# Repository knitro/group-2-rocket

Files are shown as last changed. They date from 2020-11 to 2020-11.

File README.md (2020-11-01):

# Model Rocket System
This repository contains all the files associated with the planning, design and implementation of a model rocket avionics system. 

## Hardware

### 3D Models
The folder contains the STL files for the various components that were modelled and printed for the rocket.
The parts included are:
- Gimbal
- Gimbal adaptor
- Nose cone
- Rocket body
- Rocket stand

### Avionics System
This contains the files and designs for the avionics system that will be onboard. This includes things such as the bill of materials, PCB schematics and the libraries used for the different boards.

### Base Station System
Contains the schematic and PCB layout used for the base station system. 

### Open Rocket Simulation
Contains the Open Rocket simulation for the designed rocket. In the files it contains the dimensions for the different components and weights. 

## Firmware

## Avionics System Firmware
This contains the code used for the avionics system. This includes things such as the libraries used for the different components,the test code for the different sensors and the source files for them.

### Base Station Firmware
This contains the code that will be used by the base station.

## Documentation

### Project Requirements
This contains documents which specify the requirements for the project as outlined by the stakeholder. This includes things such as the health and safety plan, lab safety plan and thorough definition of the project requirements. In the project requirement document it discusses the purpose and scope of the project, and what we planned to achieve before the end of the project.

### Architecture Design
This section contains a document which describes the architectural design of the rocket and the various systems. A proof of concept is developed using the considerations outlined in the project requirements.

### Retrospective Images
This contains the images from the retrospectives taken at the end of every sprint. In them they show what has been going well, what could be improved and other opinions of the team on this project.

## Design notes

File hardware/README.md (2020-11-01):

The software for the avionics system and base station is developed using the PlatformIO ecosystem which is built on top of the Visual Studio Code IDE. The board used by the avionics system is the Adafuit Feather STM32F405, and the board used by the base station is the Arduino Nano ATmega328.

The hardware for the avionics system is composed from several different components which have different functions. To allow for easier interfacing with the the hardware several software libraries are used. 

The different components used in the avionics system, as the libraries required are listed below:

- BMP280 (Barometer): Adafruit BMP280 Library https://github.com/adafruit/Adafruit_BMP280_Library
- BNO055 (9 Axis IMU): Adafruit BNO055 Library https://github.com/adafruit/Adafruit_BNO055
- NEO-M8N: NeoGPS https://github.com/SlashDevin/NeoGPS
- RFM95W: RadioHead Library http://www.airspayce.com/mikem/arduino/RadioHead/index.html

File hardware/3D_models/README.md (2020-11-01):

This folder contains the 3D model used to create the rocket gimbal, rocket body, nose cone and the rocket stand.

The 3D models were developed using a mixture of Solid Edge and Blender, with the files being exported as .stl for 3D printing.

All parts were printed using PLA filament, although other filaments may be preferable for increased strength. 

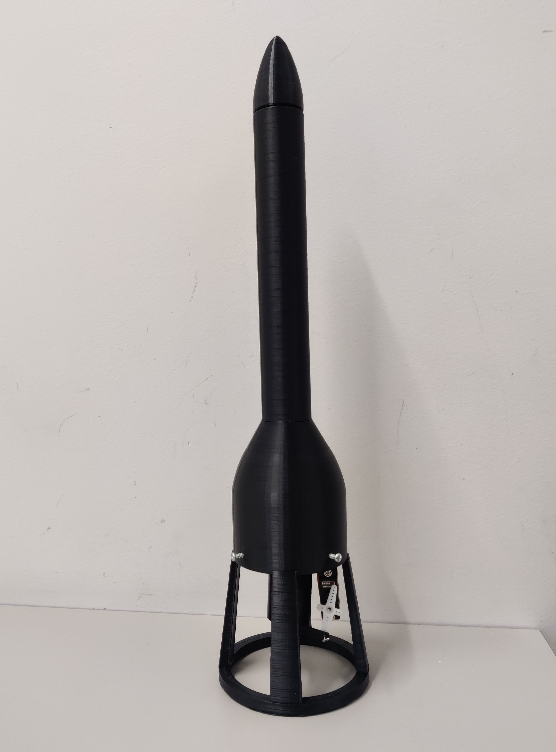
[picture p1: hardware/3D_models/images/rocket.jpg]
Assembled Rocket


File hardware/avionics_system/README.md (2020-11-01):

Throughout the project two hardware systems were developed- a prototype system and a version intended for use in the actual rocket. The prototype system was developed using a breadboard and breakout boards for initial developement and testing of code. For the second system, a schematic and corresponding PCB layout was developed, with the intention of using this design inside the model rocket. Due to time constraints, the PCB was not able to be printed and populated. Although the electronics were not assembled, all of the information required for assembly including BOM and PCB designs have been included in the hardware section of the repository.

### Pinout for prototype avionics system design:
The prototype system used an Adafruit Feather F4 in conjunction with breakout boards for the different sensors required in the avionics system. Below are the pin connections for the prototype avionics system. Note that:
- BMP280 is barometer module using SPI interface
- RFM95 is LoRa transceiver using SPI interface
- BNO055 is IMU using I2C interface
- BMP280 and RFM95 are connnected to the same SPI bus (SPI2)

| Feather Pin |  MCU Reference | Pin Function | Device Connection |
| --- | --- | --- | --- |
| A0 | PA4 | Analog in | LED |
| A1 | PA5 | Analog in | LED |
| A2 | PA6 | Analog in | LED |
| A3 | PA7 | Analog in | LED |
| A4 | PC4 | Analog in | LED |
| A5 | PC5 | Analog in | LED |
| SCK | PB13 | SPI2_SCK | SCK of BMP208 & RFM95 |
| MOSI | PB14 | SPI2_MOSI | MOSI of BMP208 & RFM95 | 
| MISO | PB15 | SPI2_MISO | MISO of BMP208 & RFM95 |
| RX | PB11 | UART3_RX | TX of NEO-M8N |
| TX | PB10 | UART3_TX | RX of NEO-M8N |
| B0 | BOOT0 | Boot0 Pin | Unused |
| SDA | PB7 | I2C1_SDA | SDA of BNO055 |
| SCL | PB6 | I2C1_SCL | SCL of BNO055 |  
| 5 | PC7 | Digital GPIO | RST of RFM95 |
| 6 | PC6 | Digital GPIO | LED |
| 9 | PB8 | Digital GPIO | INT of BNO055 |
| 10 | PB9 | Digital GPIO | G1 of RFM95 |
| 11 | PC3 | Digital GPIO (SPI Slave Select) | SPI2_SS1 of BMP208 |
| 12 | PC2 | Digital GPIO | DIO0 of RFM95 |
| 13 | PC1 | Digital GPIO (SPI Slave Select) | SPI2_SS2 of RFM95 |
| SDIO_D0 | PC8 | SD Card | SD Card | 
| SDIO_D1 | PC9 | SD Card | SD Card |
| SDIO_D2 | PC10 | SD Card | SD Card |
| SDIO_D3 | PC11 | SD Card | SD Card |
| SDIO_CLK | PC12 | SD Card | SD Card |
| SDIO_CMD | PD2 | SD Card | SD Card |
| SD_DETECT | PB12 | SD Card | SD Card |

### Pinout description for avionics system PCB design:
The table below describes the pin connections of the microcontroller and the other sensors on the avionics board. For a full connection diagram, refer to the schematic of the main avionics board.

| MCU Pin |  MCU Reference | Pin Requirements | Pin Function |
|---|---|---|---|
| 1 | VBAT | Battery input voltage (RTC) | Power |
| 2 | PC13 | Unused | - |
| 3 | PC14 | Unused | - |
| 4 | PC15 | Heartbeat LED | GPIO Out |
| 5 | PHO | Crystal input | Crystal |
| 6 | PH1 | Crystal output | Crystal |
| 7 | NRST | RESET pin | Reset |
| 8 | PC0 | Unused | - |
| 9 | PC1 | Unused | - |
| 10 | PC2 | Unused | - |
| 11 | PC3 | Unused | - |
| 12 | VSSA | Analog ground | Power |
| 13 | VDDA | Analog voltage supply | Power |
| 14 | PA0 | Battery voltage sense | GPIO Analog |
| 15 | PA1 | Reset for RFM95 | GPIO Out |
| 16 | PA2 | UART2_TX for GPS | UART |
| 17 | PA3 | UART2_RX for GPS | UART |
| 18 | VSS | Ground | Power |
| 19 | VDD | 3.3V supply | Power |
| 20 | PA4 | SPI1_NSS for Barometer | SPI |
| 21 | PA5 | SPI1_SCK for Barometer | SPI |
| 22 | PA6 | SPI1_MISO for Barometer | SPI |
| 23 | PA7 | SPI1_MOSI for Barometer | SPI |
| 24 | PC4 | IMU Interrupt 1 | External Interrupt (GPIO Input) |
| 25 | PC5 | IMU Interrupt 2 | External Interrupt (GPIO Input) |
| 26 | PB0 | SERVO 1 PWM | PWM |
| 27 | PB1 | Servo 2 PWM | PWM |
| 28 | PB2 | BOOT1 | BOOT1 pin |
| 29 | PB10 | I2C2_SCL for IMU		| I2C |
| 30 | PB11 | I2C2_SDA for IMU		| I2C |
| 31 | VCAP | Internal regulator capacitor  | Power |
| 32 | VDD | 3.3V Supply | Power |
| 33 | PB12 | SPI2_NSS for RFM95 | SPI |
| 34 | PB13 | SPI2_SCK for RFM95 | SPI |
| 35 | PB14 | SPI2_MISO for RFM95 | SPI |
| 36 | PB15 | SPI2_MOSI for RFM95 | SPI |
| 37 | PC6 | UART6_TX (Breakout) | UART |
| 38 | PC7 | UART6_RX | UART (Breakout) |
| 39 | PC8 | SDIO_D0 for SD Card | SDIO |
| 40 | PC9 | SDIO_D1 for SD Card | SDIO |
| 41 | PA8 | RFM95 Interrupt | External Interrupt (GPIO Input) |
| 42 | PA9 | USB VBUS | USB OTG |
| 43 | PA10 | USB ID | USB OTG |
| 44 | PA11 | USB DM | USB OTG |
| 45 | PA12 | USB DP | USB OTG |
| 46 | PA13 | SWDIO for JTAG | ARM_JTAG |
| 47 | VCAP | Internal regulator capacitor  | Power |
| 48 | VDD | 3.3V Supply | Power |
| 49 | PA14 | SWCLK for JTAG | JTAG |
| 50 | PA15 | Unused | - |
| 51 | PC10 | SDIO_D2 for SD Card | SDIO |
| 52 | PC11 | SDIO_D3 for SD Card | SDIO |
| 53 | PC12 | SDIO_CK for SD Card | SDIO |
| 54 | PD2 | SDIO_CMD for SD Card | SDIO |
| 55 | PB3 | SWO for JTAG | JTAG |
| 56 | PB4 | Unused | - |
| 57 | PB5 | Eject 1 for Parachute | GPIO Output |
| 58 | PB6 | Eject 2 for Parachute | GPIO Output |
| 59 | PB7 | Eject 3 for Parachute | GPIO Output |
| 60 | BOOT0 | BOOT0 for programming | BOOT0 |
| 61 | PB8 | Unused | - |
| 62 | PB9 | SD_DETECT for SD card | GPIO Input |
| 63 | VSS | Ground | Power |
| 64 | VDD | 3.3V Supply | Power |

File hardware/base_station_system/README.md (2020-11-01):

A prototype base station system was developed in conjunction with the developement of the prototype avionics system. This system simply consists of an Arduino Uno board connected to a RFM95 LoRa module for communication with the avionics system.

### Pinout for base station prototype:

Below shows the pin connections of the base station. It simply consists of a RFM95 transceiver module connected to an Arduino Uno/Nano (or compatible) via an SPi interface.

| Arduino Pin | MCU Reference | Pin Function | Device Connection |
| --- | --- | --- | --- |
| 13 | PB5 | SCK | SCK of RFM95 |
| 12 | PB4 | MISO | MISO of RFM95 |
| 11 | PB3 | MOSI | MOSI of RFM95 |
| 10 | PB2 | SS | CS of RFM95 |
| 9 | PB1 | Digital GPIO | RESET of RFM95 |
| 3 | PD3 | Digital GPIO | DIO1 of RFM95 |
| 2 | PD2 | Digital GPIO | DIO0 of RFM95 |

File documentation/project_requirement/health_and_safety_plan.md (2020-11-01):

# ENGR 301: Safety Plan Living Document

## Introduction:

The aim of this document is to layout the safety plan draft for the avionics system Group 2 will build. This will include listing the project requirements that create risk of bodily harm, and the plan to mitigate those risks.

This is to be adjusted according to changes in the working environment, as well as the wider society. Due to unsettling times resulting from COVID-19, health and safety should be of most concern, even if the situations that we may be in are constantly changing within both the context of the project, and our own personal lives. *See section 2 for more details.*

## Contents:

1. **The Rocket**
2. **COVID-19**
    * 2.1 Alert Level 1
    * 2.2 Alert Level 2
    * 2.3 Alert Level 3
    * 2.4 Alert Level 4
3. **Launch Details**
    * 3.1 Travel Plan
    * 3.2 Environment
    * 3.3 Equipment
    * 3.4 Supervision
    * 3.5 Launch
    * 3.6 Unforeseen Events
        * 3.6.1 Members of the public
        * 3.6.2 Faulty Components and Equipment
4. **Appendices**
    * Appendix A: Risk and Mitigations
    * Appendix B: CAA of NZ Regulations Part 101.7
5. **Bibliography**

## 1. The Rocket:

As of this stage, the specific form of the rocket is undeterminable; however, general aspects that the rocket have been outlined, and safe procedures for those aspects determined.

The rocket will use either an electric or solid-fuel motor; in the case of the solid fuel motor, additional risks are presented. The solid fuel motor used, of which is limited to the C and D classifications, is obtained as a complete certified product by the given manufacturer. The motor will not be modified, or used, in any way other than that outlined by the manufacturer. The engine must never be exposed to any ignition source other than that of the launch platform, and for this case, only when carrying out the launch event. Only an electrical ignition system can be used for the ignition of the rocket, as per the NZ Rocketry Association's safety code for rockets utilizing class A-F motors.

The rocket's expected maximum altitude after launching has not yet been determined. The distance the rocket may drift after launch, due to wind, may resultantly not be determined. Regardless, an exclusion zone around the rocket launch site must be established before launching; only personnel directly tasked with the launch of the rocket may be permitted within this zone. Minimizing the risk to non-vital personnel is paramount.

The NZ Rocketry Association's safety code also states that materials used for exterior features of the rocket (nose, body, and fins) must be lightweight and non metal. This is to minimize potential injury in the event that the rocket falls, or otherwise collides, with a person.

## 2. COVID-19:

An issue that has arisen during the initialization of this project has been COVID-19. This situation is evolving as the newly introduced COVID-19 Alert System [1] forces changes upon the workflow on the project. To plan and comply with each alert system, the guidelines below must be followed by all team members on top of any requirements from the official alert system [1], and any other requirements listed in this document.

### 2.1. Alert Level 1:
*Prepare Stage: The disease is contained in New Zealand* 

* Any team member who feels unwell should stay home immediately, while contacting everyone else in the team to let them know. A time when they started to feel ill should be disclosed during this contact.
* When meeting in person, all team members must engage in physical distancing as per the recommended from the NZ Government.

### 2.2. Alert Level 2:
*Reduce Stage: The disease is contained, but the risk of community transmission remains*

* Everything from Alert Level 2 and..
* All launches must be performed where nobody else from the public is present.

### 2.3. Alert Level 3:
*Restrict Stage: High risk the disease is not contained*

* Everything from Alert Level 2 and below and ..
* All project work must be done online with no exceptions.
* All meetings must be performed online.
* Any launches are to be postponed until a lower alert level is reached. 

### 2.4. Alert Level 4:
*Lockdown Stage: Likely that disease is not contained*

* Everything from Alert Level 3 and below and ..
* Requirements and deadlines to be extended to assist in the mental health of all team members from the stress.

## 3. Launch Details:

An issue that has arisen during the initialization of this project has been COVID-19. This situation is evolving as the newly introduced COVID-19 Alert System [1] forces changes upon the workflow on the project. To plan and comply with each alert system, the guidelines below must be followed by all team members on top of any requirements from the official alert system [1], and any other requirements listed in this document.

### 3.1. Travel Plan:

To ensure the safe transportation of all team members and the rocket, the procedures listed must be followed:

**Team Members:** <br>
* A designated university staff member must be contacted prior to the travel, citing exact time, date and location of the launch, and the arrival time after the launch.
    * The contact details must be readily available for all team members.
* Time, date and the location of where we are going to launch must be written in the Mattermost for everyone to reference against.
* There must be an established meeting place for the situation where any member is lost. This location must be determined, and known to all members, prior to the rocket's launch.
    * This meeting place must have reception and/or internet connection that is accessible by all team members. This is to ensure everyone present is able to make contact with appropriate team members or university staff.
* Everyone must be able to contact each other through mobile means (such as text/messenger apps) in the case that a team member is missing.
    * If contact through these means is unavailable (such as lack of reception), then everyone must meet at the designated meeting place.
* In the event that it is unavailable to meet with or contact a team member, the designated university staff must be contacted to explain the situation.
* If the team members do not arrive at the specified time, the designated university staff must take emergency action.

**Rocket:** <br>
* The rocket must be transported, such that the engine is not ignited during transport.
    * [Engine specifications here with heat that the engine combusts, ways to mitigate this]
* The rocket must be transported, such that the rocket does not injure anyone through physical contact.
    * This is to be resolved through transporting the rocket such that the rocket should not be able to be moved while in transport.
    * [Add exact transportation implementation of the rocket here]

### 3.2. Environment:

All relevant regulations must be met to ensure that the rocket launch is as safe as possible for the team members, as well as the wider community and environment. These include the following:
* CAA 101.157 - The rocket shall not be launched given that there are clouds that cover more than half of the sky (See Appendix B)
* CAA 101.158 - The rocket should not be launched during the night (See Appendix C)

To ensure these regulations are met, the following assessment of the environment must be performed before launch:
* The rocket is to be only launched during the day, with more than half of the sky being visible, and not obstructed by clouds.
    * This is to ensure the rocket's location, regardless of GPS tracking, can be observed and followed during the entire rocket launching process.
* Check for any precipitation. The presence of any will lead to the cancellation of the launch. 
    * This is due to the possible case that the precipitation disallows the rocket to successfully launch, creating a situation where the rocket has not launched when expected.
* Wind speeds and gusts must be checked to not exceed ([some_value] km/h, [some_value] km/h). 
    * This is due to the possible case that the ignited rocket will spread the ignition flames to uncontrollable levels.
    * This is also to ensure that the rocket is still able to have a controlled ascent up, and descent down, without leaving the specified premises.

Wind Speeds, weather and precipitation chance data are all to be collected via the AccuWeather and MetService before launch day, and before launch. 
*  https://www.accuweather.com/
*  https://www.metservice.com/
If the weather does not permit and/or appear to not be permittable (such as high chance of precipitation) during any of these stages, the launch should be cancelled or postponed immediately.

To avoid any damage in the environment where the launch is taking place, it must be ensured that:
* The area is clear of anyone else other than team members and/or other supporting staff.
* The area around the rocket launching position must be clear of debris.
* The area that the launch of the rocket is taking place must be clear from any obstructions that may cause disruptions if interacted with, such as powerlines.
* Potential landing areas downwind from the launch site must be free of obstructions that could be damaged and/or interact with the rocket. The potential landing area must be calculated before each launch, taking into account dynamic factors such as wind speed, rocket motor burn time, expected altitude and other factors. The landing area will be extremely large so that safety is not at risk and the ability to recover the rocket is almost ensured.

If any of these conditions cannot be fully met, the launch must be postponed or cancelled entirely.

To ensure no member of the public walks in during the launch sequence, or during flight, there shall be 3-4 team members covering all possible entrances at the maximum distances into the launch site, advising and ensuring nobody enters until the launch has finished.
If anybody disregards these orders for any reason, the launch must be cancelled or postponed if the launch has not been performed yet.

### 3.3. Equipment

The following equipment is to be taken to the launch. These must all be checked off prior to, during, and after being at the launch site. This is to ensure all items are accounted for, and that any dangerous or safety related equipment for other teams are still available for use, and aren't left as a risk to the general public.

| Equipment 	| Owner 	| Purpose |
|---	|---|--- |
| Rocket 	| ? 	| To ensure we have something to actually launch. |
| First Aid Kit 	| School of Engineering and Computer Science at Victoria University of Wellington 	| This is to assist in the case of an injury from a team member, or a member in the public. |
| Fire Extinguisher 	| School of Engineering and Computer Science at Victoria University of Wellington 	| This is to assist in the case of a fire. |
| Hi-Vis Vests 	| School of Engineering and Computer Science at Victoria University of Wellington 	| This is to assist in finding and distinguishing team members so that they are visible at all times. |
| Safety Goggles 	| School of Engineering and Computer Science at Victoria University of Wellington 	| This is to ensure the protection of all participants eyes from fires, explosions or transport of potentially dangerous materials 	|
| Personal Mobile Phones 	| Team Members 	| This is for communications and checking weather. |
| Rail Launch Pad 	| ? 	| This is to ensure the stability of the rocket prior to launch. |
| Laptop 	| Team Members 	| This is such that data is able to be intercepted, and recorded from the rocket's antenna. It is also used for checking weather data. |
| Ignition Switch 	| ? 	| This is so the rocket is able to be launched. 	 |
| Tool Kit | School of Engineering and Computer Science at Victoria University of Wellington | This is to ensure in the case the rocket is damaged, it can be repaired. |
| Spare Repair Gear for the Rocket | ? | This is to ensure in the case the rocket is damaged, it can be repaired using the spare repair gear. | 

### 3.4. Supervision

All launches will be supervised by the client. The client for this design and is a member of the NZ Model Rocketry Association.
The client will be responsible for approving the launch and launching the rocket, no one else may launch the rocket. All motors and propellant will be transported to and from the launch site by the client. The rocket will be launched from a launch pad and rail provided by the client.

### 3.5. Launch

The launch of the rocket poses multiple risks to team members, and members of the general public; minimizing these risks is paramount.

In accordance with the NZ Rocketry Association, individuals are free to launch rockets using class A to D motors, provided they have the permission of the owner of the launch site. No greater authority needs to be informed of the rocket's launch.

The immediate launch site must be safe from hazards before a launch may be prepared; this includes direct (e.g. sharp objects) and indirect (e.g. flammable materials) hazards that may harm team members. In these conditions, members of the general public should not be present; however, these hazards should be considered as potential risks for the general public as well.

Solid fuel motors pose the greatest risk at launch; flammable debris, such as dry grass, may ignite as a result of the motor's burn. The immediate area within 3m of the launch pad must be clear of any flammable materials. If this is not achievable, a fire resistant deflection material may be place immediately underneath the launch pad. All personnel must wear suitable PPE in preparation for the launch; namely safety glasses.

Personnel related to the rocket launch should be clear of the rocket at the time of launch. When the area is deemed clear of hazards, and all personnel safely distanced from rocket, a countdown will commence to make all personnel aware of the eminent launch. This countdown will provide a generous, and safe amount of time for all personnel; any member of the team may cancel the launch at any point during the countdown, at which point the safety interlocks will be re-enabled.

In the event of a misfire, launch pad safety interlocks must be enabled. The rocket is not to be approached for at least 60 seconds, at which point only the client may approach the launch pad for inspection.

### 3.6. Unforeseen Events

#### 3.6.1 Members of the Public

To ensure the safety of the members of the public, the following must be performed:
* Any member of the public entering the premises of the launch must be stopped by a team member to the best of their ability. If the closest team member is unable to communicate with that member of the public under any circumstance, another team member must approach the given member of the public to discuss about the rocket launch, and inform them of the associated risks.
* If a member of the public would enter the premise of the launch site, the launch must be postponed until the member of the public leaves the premises.
* If a member of the public is unwilling to listen to the team member, the client must be contacted ASAP to discuss the situation with the member of the public.
* If, for any reason, a member of the public decides to not listen to the warnings and communications of the team members, either actively or inactively, the launch of the rocket must be postponed if possible, until the issue is resolved with the client and the member of the public.

#### 3.6.2 Faulty Components and Equipment

To ensure the safe launch of the rocket, the following procedures must take place if there appears to be faulty equipment:
* If the rocket is physically damaged/suspected to have sustained damage during transportation, the motor must be removed before being inspected.
    * If the rocket has sustained physical damage, it must be determined if the rocket is still safe to launch or not. If the rocket can not be suitably repaired in-the-field, such that it could perform identically to how it would have prior to the damage, the launching of the rocket must be postponed until proper repairs have been completed.
    * If any electronics are broken alongside the physical body of the rocket, then the launch is to be postponed until the fix can be made.
    * If the fix cannot be made to either the physical rocket or the electronics, the launch is to be cancelled until further notice.
* If anything corresponding to the launch is faulty (such as failure of motor ignition or lack of combustion), all members near the launch must promptly relocate to a designated protected area, wait a minimum of 2 minutes, and then allow the client to approach and assess the situation.

## 3.7 Lab Risks:

When constructing the rocket in the lab, there are several important risks to account for.

* When working on computers for coding, regular breaks must be taken to reduce the chances of repetitive strain injury (RSI) and any strains to the eyes.
* When creating the rocket, the working area must be clean. This means that:
    * The floors must be clean such that cables and wires do not trip anyone up.
    * Furthermore, there should not be any sharp objects on the ground in case anyone does trip.
    * There must be sufficient air flow when soldering, such as a room air conditioning and a small fan at the soldering station.
    * Contact to wall outlets/230VAC supply should never be made under any circumstances; connections to these outlets should never be exposed.
    * The maximum voltage of any circuit, under prototyping conditions or other, should never exceed 60V.

# 4 Appendix:

## Appendix A:
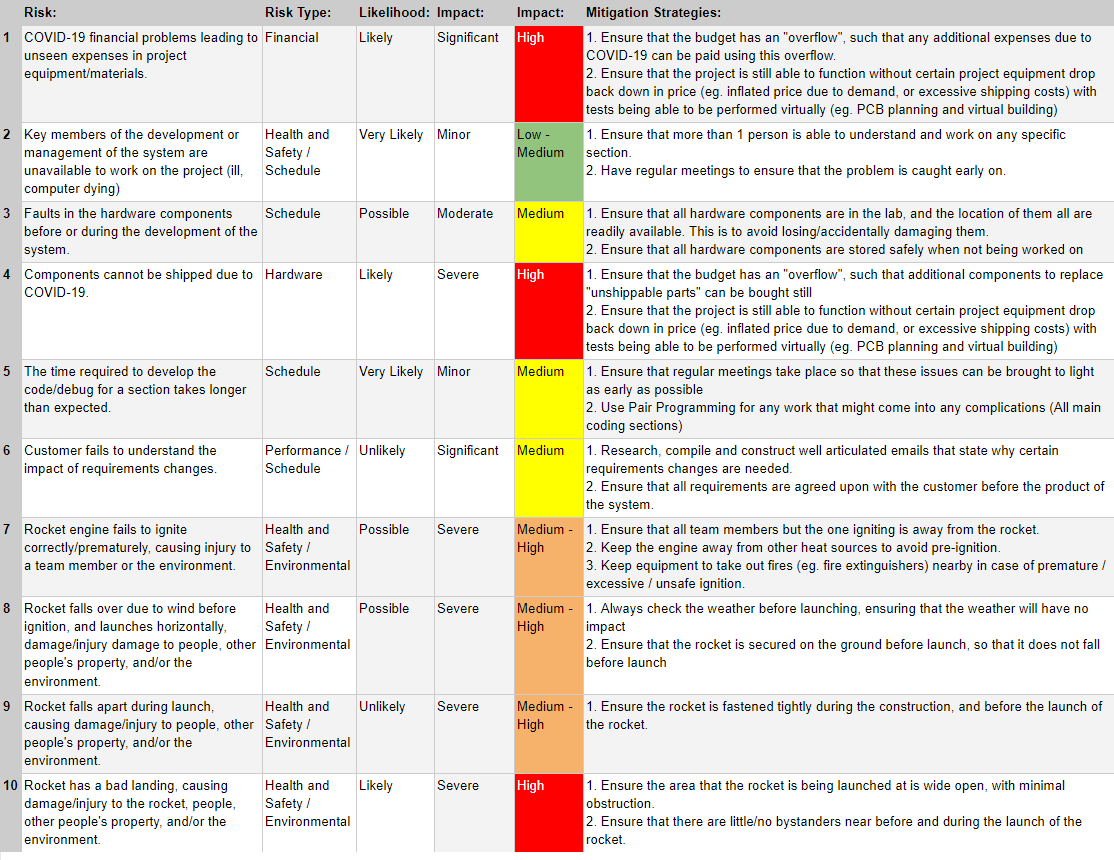
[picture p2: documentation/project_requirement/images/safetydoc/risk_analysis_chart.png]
Appendix Image


## Appendix B:
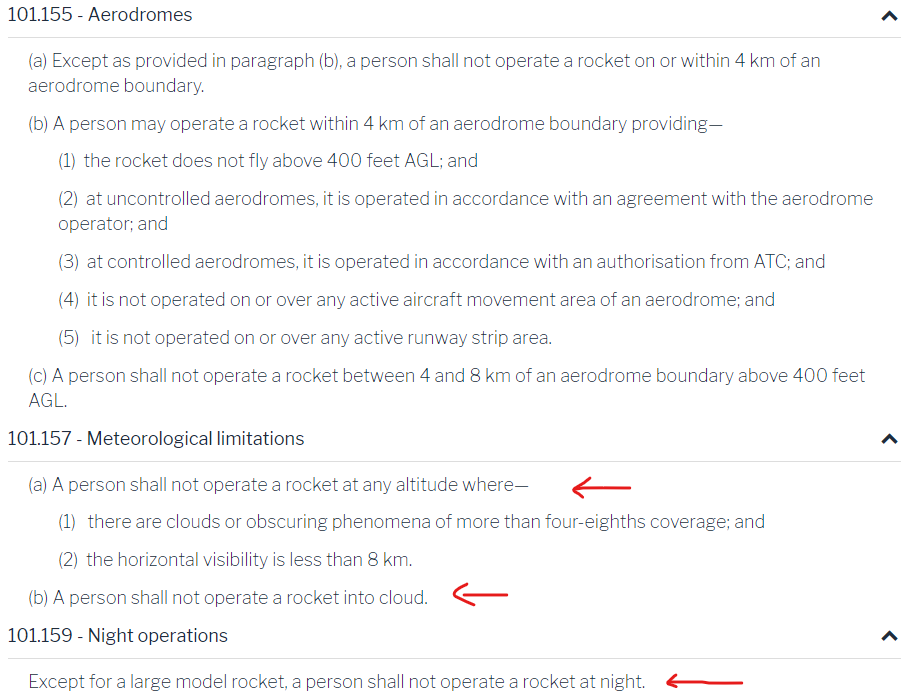
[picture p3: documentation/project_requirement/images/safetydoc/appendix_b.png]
Appendix Image


# 5. Bibliography: <br>
[1] https://covid19.govt.nz/alert-system/
[2] https://www.nzrocketry.org.nz/rocketry/rocket-safety

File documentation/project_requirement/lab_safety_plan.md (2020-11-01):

# Lab Safety Plan

*Last Update: 07/08/2020*

## Introduction

The aim of this document is to layout a Health and Safety Plan for the hardware development of the rocket.
The development of the rocket hardware poses several risks that need to be mitigated in order for the health and safety of not just the members in Group 2, but also any other personnel in the laboratory and/or in the wider building.

**This document will endeavour to:**

* Identify the risks present when working in a laboratory environment, and in particular when developing an avionics system for a rocket
* Identify the mitigating factors and controls that will reduce these risks identified above

This document will build on the general safety plan already specified by the laboratory rules to provide more specific guidelines to be followed by all members involved.

---

## Contents

1. **The Rocket**
2. **Risk Matrix**
3. **Control Plan**
    * *3.1:* Soldering Irons
    * *3.2:* Sharp Objects
    * *3.3:* Mechanical Tools
    * *3.4:* Moving Parts
    * *3.5:* Exposed Circuits
    * *3.6:* Overuse/Fatigue
    * *3.7:* Cables/Foot Hazards
    * *3.8:* 3D Printers
    * *3.9:* Powered Equipment
4. **Appendices**

---

## 1. The Rocket

The purpose of this project is to develop and test a rocket that is capable of making a controlled ascent. This document will address the risks associated with the development and testing of the rocket in a laboratory environment. There will be no testing of the rocket propulsion or parachute ejection in the laboratory, and as such this document will not address the risks relevant to those tests. The rocket will include a motorized gimbal, exposed circuits, and connecting wires and hence this document will address the risks associated with developing and testing these components.

---

## 2. Risk Matrix

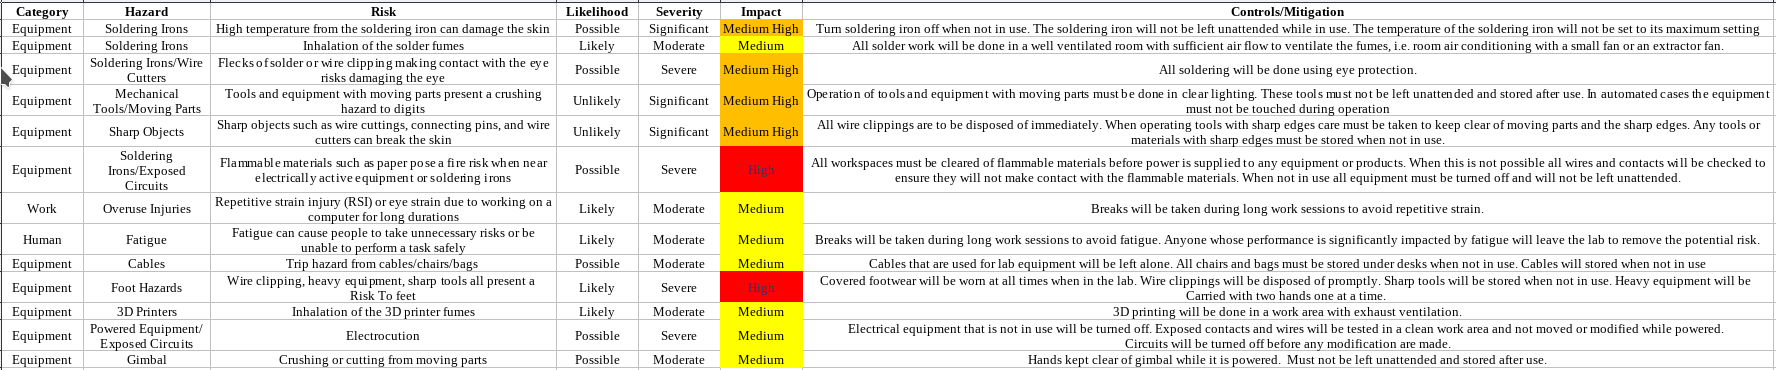
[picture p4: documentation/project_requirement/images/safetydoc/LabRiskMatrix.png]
Laboratory Risk Matrix


---

## 3. Control Plan

This control plan will describe the implementation of the control factors described in the risk matrix and where to report incidents that do occur.

The term *'session'* is used to denote the duration of an activity, not the entire time spent in the laboratory.

It is important to note that the development of the rocket will occur in and only in CO249. This is to make sure that if any incidents occur, everyone will know where the problem has occurred and assist appropriately. 

### 3.1 Soldering Irons

Use of soldering irons carries some risks as listed in the risk matrix.

One designated team member will be assigned at the **start of each session** to be responsible for:

* Ensuring appropriate ventilation during operation.
* Ensuring the work station is clear of flammable materials.

During the operation, the user of the soldering iron should

* Check the temperature settings to confirm that it is not set too hot.
* Ensure that they are educated enough to be fully confident to use a soldering iron.

This team member will also be responsible at the **end of each session** to:

* Turn off the soldering iron at the end of each session.
* Ensure the soldering iron is not stored near flammable materials.

 All team members in proximity of the operation of the soldering iron must wear eye protection.

If someone suffers a burn from the iron, irritation from the fumes, or their eye is contacted by hot solder flecks an incident report will be filled in and sent to Roger Cliffe (ecs-safety@ecs.vuw.ac.nz) with a CC to Aaron Chen (aaron.chen@vuw.ac.nz) and Craig Anslow (craig.anslow@vuw.ac.nz).

### 3.2 Sharp Objects

Sharp objects that may be involved in the laboratory include wire cutters and wire clipping. What is written here applies to other sharp objects that may or may not be involved in the design and testing of the Rocket. In the case of sharp tools such as wire cutters, care will be taken to ensure digits are clear of the edge during use.

A team member will be assigned at the **start of a session** to:

* Ensure that any sharp tools are put away when not in use.

In the case of sharp debris such as wire clippings, the same or another team member will be assigned at the start of the session to:

* Dispose of the debris as soon as they are produced.

When doing any activities involving sharp objects, including cutting/stripping wires all team members in close proximity should wear safety glasses.

If someone suffers from an embedded object and/or bleeding, an incident report will be filled in and sent to Roger Cliffe (ecs-safety@ecs.vuw.ac.nz) with a CC to Aaron Chen (aaron.chen@vuw.ac.nz) and Craig Anslow (craig.anslow@vuw.ac.nz).

### 3.3 Mechanical Tools

Tools with moving parts that are operated manually will be done in clear lighting and care will be taken to keep digits clear of moving parts.

In the case of automated tools being used, a team member will be assigned to:

* Monitor the process entire process.
* Ensure that the automated tools are not touched by anyone while in operation.

If someone suffers from crushed digits an incident report will be filled in and sent to Roger Cliffe (ecs-safety@ecs.vuw.ac.nz) with a CC to Aaron Chen (aaron.chen@vuw.ac.nz) and Craig Anslow (craig.anslow@vuw.ac.nz).

### 3.4 Moving Parts

Moving parts of the Rocket include the motor controlled gimbal.

**Before any testing occurs**, a team member must be assigned to:

* Monitor the gimbal for the entire duration of the test.
* Ensure that any moving parts will not be touched by anyone until the test is complete and the power is removed.

If someone suffers from crushed digits an incident report will be filled in and sent to Roger Cliffe (ecs-safety@ecs.vuw.ac.nz) with a CC to Aaron Chen (aaron.chen@vuw.ac.nz) and Craig Anslow (craig.anslow@vuw.ac.nz).

### 3.5 Exposed Circuits

The avionics control system is controlled by different modules that have exposed contacts.

**At the beginning of a session** a team member will be assigned to:

* Clear the work area of flammable materials before the circuit is powered.
* Ensure that all parts that contain exposed contacts when powered on are not to be touched until they are turned off.

If someone suffers electrocution or burns an incident report will be filled in and sent to Roger Cliffe (ecs-safety@ecs.vuw.ac.nz) with a CC to Aaron Chen (aaron.chen@vuw.ac.nz) and Craig Anslow (craig.anslow@vuw.ac.nz).

### 3.6 Overuse/Fatigue

To avoid potential errors or injury resulting in overuse/fatigue, a team member will be assigned at the **start of a session** to:

* Keep track of the current time.
* Keep track the time that any one team member has been working for.

Should any team members work for over an hour without a break they will be asked to have a 5 minute break from any development.

If someone suffers from a repetitive strain injury or makes an error due to fatigue an incident report will be filled in and sent to Roger Cliffe (ecs-safety@ecs.vuw.ac.nz) with a CC to Aaron Chen (aaron.chen@vuw.ac.nz) and Craig Anslow (craig.anslow@vuw.ac.nz).

### 3.7 Cables/Foot Hazards

To avoid causing harm to any one self or another team member of laboratory personnel through tripping or any other foot hazards, a team member will be assigned at the **start of the session** to:

* Ensure that all the walkways in the laboratory are clear of tripping hazards on the floor.
* Tripping hazards include but are not limited to cables, bags, and chairs.
  
It is each team members responsibility to attend sessions wearing covered footwear.

If someone suffers from a fall or harms their foot an incident report will be filled in and sent to Roger Cliffe (ecs-safety@ecs.vuw.ac.nz) with a CC to Aaron Chen (aaron.chen@vuw.ac.nz) and Craig Anslow (craig.anslow@vuw.ac.nz).

### 3.8 3D Printers

To ensure that a 3D printer does not present a fire or health risk a team member will be assigned at the **start of a session** to:

* Ensure that the extraction ventilation is functioning properly.
* Monitor the 3D printer to ensure it does not catch fire.
* Confirm that the 3D printer is turned off at the end of the session.

If someone suffers from irritation from the fumes an incident report will be filled in and sent to Roger Cliffe (ecs-safety@ecs.vuw.ac.nz) with a CC to Aaron Chen (aaron.chen@vuw.ac.nz) and Craig Anslow (craig.anslow@vuw.ac.nz).

### 3.9 Powered Equipment

Powered Equipment refers to any equipment that supplies or is supplied electricity that was not previously referred to.

 **At the start of a session** a team member will be selected to:

* Ensure the equipment does not pose a fire risk by removing flammable materials from the work area.
* Ensure the contacts of the powered equipment are not to be modified/added/removed until turned off.
* Check that the equipment has been turned off at the end of a session.

If someone suffers from electrocution an incident report will be filled in and sent to Roger Cliffe (ecs-safety@ecs.vuw.ac.nz) with a CC to Aaron Chen (aaron.chen@vuw.ac.nz) and Craig Anslow (craig.anslow@vuw.ac.nz).

---

## 4. Appendices

*None Yet*

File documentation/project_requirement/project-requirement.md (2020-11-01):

# ENGR 301 Project 2 Project Proposal and Requirements Document

## 1. Introduction

Amateur rocketry is a hobby that is popular throughout the world. These rockets are typically powered by off the shelf rocket motors which are available in a number of different classes. Smaller rockets will typically reach speeds up to Mach 1, and altitudes of 100-500m. These rockets are usually composed from lightweight materials such as wood, cardboard and plastic. Larger rockets can reach a speed several times the speed of sound, and an altitude of several kilometres. The larger rockets tend to be made from materials such as fibreglass and aluminium due to the larger forces exerted on the rocket body.

Most rockets have a passive control system consisting of fins which help to stabilise the rocket during flight. When implemented correctly, this method of controlling a rocket is simple and reliable, but it cannot correct for external disturbances. Wind is the main external disturbance that will effect the trajectory of a rocket, and the implementation of an active control system can negate the wind's effect on a rocket. Additionally, an active control system can make adjustments to correct for any imperfections in the construction of a rocket and motor. An active control system will necessarily make a rocket more complex and heavier, but it has the significant benefit of controlling the rockets trajectory precisely. A more accurate trajectory results in higher altitudes and more predictable landing zones, which are the main drawback of the traditional passive control system.

### Client

*Removed*

### 1.1 Purpose

The purpose of this system is to provide active control and gather telemetric data within the lower atmosphere using a solid-fuel rocket as defined by the customer. The system will resolve the issues associated with a passive control system, such as the effect on wind on rocket trajectory.

### 1.2 Scope

### The Avionics Component of the System should meet the Following Goals

- When the rocket moves, the system shall adjust the gimbal via a PID controller and control the rocket thrust vector accordingly.
- Every 3 seconds, telemetry (velocity, acceleration, GPS position, altitude, temperature) shall be collected by the system.
- When telemetry (as stated above) is collected, the system shall record it on the system's storage. This is to be finished before the next telemetry is given to be processed.
- When telemetry (as stated above) is collected, the system shall transmit the telemetry to the base station over a wireless channel and be successful before the next telemetry is given to be processed.
- The system shall be in a small physical form factor, such that is it smaller than the previous 2018 and 2019 rockets.
- The system shall be physically modular so that any part of the system can be easily replaced when damaged or becomes faulty without more than 10 minutes work.

### The Base Station Component of the System should meet the Following Goals

- The base station shall receive telemetry from the avionics package over a wireless channel whenever the avionics package sends data. The data contain no more than 5 errors when being transmitted.
- The base station shall be able to output all the data it receives and processes to the computer over a serial USB connection. This shall be in a format that is easily readable by humans.

The system will be used to actively control solid fueled rockets, and to record and transmit telemetry

### 1.3 System Overview

#### 1.3.1 System Context

Current amateur rocket designs use passive control systems with onboard telemetry to analyse a rocket's behaviour. The aim of the avionics system is to actively control the rocket to allow it to launch from many different situations, such as a high altitude balloon or a boat. The system will be able to account for non-ideal launch conditions such as high wind, making rocket launches easy and safe. Furthermore, the active control system will allow the user to modify the flight path of the rocket to account for the wind. This will allow a rocket to be easily recovered, and reduces the sizes of launch site required.

In addition to active control, the avionics package will record and transmit telemetry from the rocket to the base station, which will be connected to the user's computer. This allows the user to monitor the velocity, altitude and GPS location of rocket in real time. The real time GPS location data sent by the avionics system will allow the user to find the landing site of the rocket.

The block diagram below shows an overview of the required components in the avionics part of the system. The avionics system requires a microcontroller which will control all the other components in the subsystem. The inertial measurement unit (IMU), GPS module, battery and radio receiver are inputs into the microcontroller, while the motor gimbal, radio transmitter, SD card and parachute deployment mechanism are controlled by the microcontroller outputs.

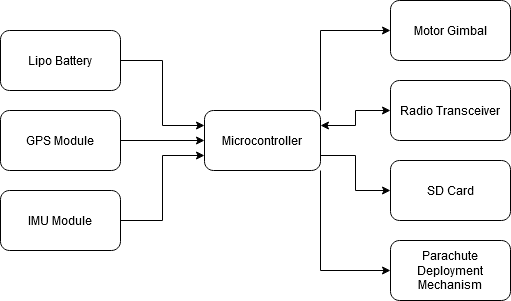
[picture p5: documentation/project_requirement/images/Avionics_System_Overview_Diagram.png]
Avionics System Overview Diagram


The base station subsystem has the required components as defined in the block diagram below. The radio receiver will send data into the microcontroller, which will in turn send the data to the computer where it will be viewed by the user through a software interface. Similarly, a human will send control commands through the software interface, into the microcontroller which will then send this data to the avionics system through the base station's radio transmitter.

Base Station System Overview Diagram

Both the avionics system onboard the rocket and base station will have a software component which will allow two-way communication. This software system will allow the transmission of commands to the rocket. It will also allow the transmission of some limited logging information and sensory readings to be sent in realtime back to the base station. This data can then be relayed to the mission control software.

#### 1.3.2 System functions

##### 1.3.2.1 Minimum Viable Product

The minimum viable product encompasses a solid-fuel or electric engine propelled rocket with active flight control and course correction; the product must be able to launch from a provided launch-pad and display autonomous control for the entirety of its flight, with flight termination occurring at the expenditure of fuel/power. The rocket's flight control scheme must incorporate an integrated control board and gimbal mount for the engine. An accelerometer should be used to provide feedback to control software, adjusting the engine's direction of thrust to correct, and maintain, controlled flight.

The final product will be extended to function beyond the minimum viable product, as below:

##### 1.3.2.2 Avionics Package

The main functions of the avionics system are outlined below:

- **Active Control System:** The main purpose of the avionics package is to actively control the rockets trajectory. The avionics system will be able to control the rockets trajectory through the use of servo motors which will adjust the thrust vector of the rocket engine. The avionics system will use the onboard telemetry data in conjunction with a PID control system to precisely control the path of the rocket. The user will be able to define the flight path of the rocket to account for external factors such as wind. The control system will be in charge of deploying a parachute (or similar) which will allow the rocket to gradually fall back to the earth. The control system will need to use the sensory data available to determine the optimal time to deploy the parachute.

- **Black Box Recording:** The avionics package will have on board storage (such as a micro SD card) which will store all of the relevant telemetry including altitude, velocity, location, air pressure and acceleration at frequent intervals. The data stored on the SD card will be formatted so that it can be easily imported into a spreadsheet software such as Excel for further analysis by the user. The system should be designed in such a way that if there is an abnormal event, data is available to determine the cause of the failure. This will involve ensuring the data will survive the abnormal event (such as a crash).

- **Telemetry Transmission:** The avionics package will have an onboard transceiver which will be capable of sending telemetry back to the base station in real time. This will allow the user to monitor the rocket's status during the flight. Additionally, the avionics will be capable of sending the location of the rocket back to the base station, which will allow the user to easily recover the rocket once it has landed. Furthermore, communication to the rocket from the user will be supported.

##### 1.3.2.3 Base Station

The main functions of the base station system are outline below:

- **Human Control:** The base station will contain a transceiver which will be capable of receiving data from the rocket, and transmitting data to the rocket. The transmission of data to the rocket will allow the user to control some of the rocket parameters, such as trajectory or telemetry recording frequency. The transmission system will also allow the user to remotely launch the rocket from the base station.

- **Telemetry Reception:**
The base station system will be able to receive live telemetry from the rocket through its radio transceiver. The base station will then forward this data through a serial USB connection to a computer in a format comma separated format. This will allow the mission control software to display a live feed of the rockets status (acceleration, velocity, altitude).

- **GPS Assisted Recovery:**
The telemetry reception capabilities of the base station will allow it to receive the current GPS location of the rocket. This will allow the user to perform GPS-assisted recoveries of a rocket. This will be essential for rocket recovery when the launch site is not an ideal location (e.g. lots of trees/hills). It is important that the rocket transmits this location data while it is flying, as it may not be able to receive a satellite signal once it has landed.

#### 1.3.3 User Characteristics

In accordance with the request of the client, all information associated with this project is open source, and is thus available to the wider rocketry community. Users are expected to have significant experience in the field of model rocketry, but the design does not assume experience with implementing an active control system within a rocket. This opens access to users looking to use this unit as a first time solution to adding an active control system to a rocket. For this reason, the avionics system and base station needs to be designed so that the installation process is simple for a beginner. Similarly, the documentation of both sub-systems should be thorough to assist a user in the installation and operation of the system. As the project is open source, some advanced users may wish to modify the system (schematic, PCB, source) to suit their specific requirements. This further enforces the need for thorough documentation to allow a user to make modifications easily. Typically, the avionics system and base station would be implemented in a model rocket, but few users may utilize the system for other applications. These users would be advanced users with a lot of technical expertise, so would need little guidance in the using the system in their unique application.  

Since model rockets are the primary intended application of this unit, experience in the field of model rocketry is required from users. This ensures the safety of the user, the environment and others. Specifically, users must be:

- Familiar with the processes involved in the safe launch and recovery of a model rocket
- Familiar with the CAA (Civil Aviation Authority) regulations, in particular the Part 101 rules for unmanned aircraft [1]
- Physically capable of operating a rocket with an avionics system in a safe way

Additionally, international users (not based in New Zealand) must ensure the frequency and power of the radio transceiver is allowed in their specific country, to ensure they follow regulations and do not interfere with other important signals

With these user constraints in mind, there are two main user groups that this unit is likely to be useful to:

- Model rocket hobbyists who are inexperienced with active control systems, seeking an all-encompassing solution to incorporate active control, black box recording and telemetry transmission systems into a rocket.
- Rocketry hobbyists or professionals who are more experienced with active control systems, looking for an active control solution that they can modify to suit their own needs, or iterate upon for community benefit.

#### 1.3.4 Limitations

##### 1.3.4.1 Regulatory Policies

**Radio Frequency Restrictions:** The system will be designed to comply with the radio frequency restrictions managed by the Radio Spectrum Management (RSM) unit of the Ministry of Business, Innovation and Employment (MBIE) in New Zealand [2]. Therefore, the system produced may not be suitable for use in other regions due to different radio frequency allocation. If users wish to implement this systems in other countries it will be their responsibility to ensure they comply with local radio frequency regulations.

**Aviation Authority Regulations:** The system is intended to actively control a model rocket. The system will be designed to comply with the CAA (Civil Aviation Authority) regulations in New Zealand for unmanned vehicles. The avionics and base station systems may not be compliant with the aviation regulations regarding unmanned vehicles in other countries. As a result, users in some regions may be unable to legally use the system.

##### 1.3.4.2 Hardware Limitations

**GPS Signal Strength:** The system is designed with the assumption that the area will have a sufficient number of GPS satellites that the GPS module can connect to. Some locations may have few satellites with sufficient power to be picked up by the GPS module, in which case it may not be possible to determined the location of the avionics system. The system will be designed to with the capabilities to pick up a GPS signal in Wellington. In locations where GPS signals are not easily obtained due to the environmental conditions (terrain, location) the GPS assisted recovery function will not be reliable. This issue could be mitigated by including a high gain antenna or amplifier in the system, but these measures will greatly increase the size and the weight of the system. For this reason, the system will be designed to suit the majority of applications.

**Radio Bandwidth/Range:** The bandwidth of the communications system that connects the base station and avionics system will differ depending on the signal strength and the distance between the base station and avionics system. For some launch locations, the geography of the surrounding area will have an effect on the strength of the signal. Similarly, some rockets may reach very high altitudes which necessarily increases the range between the base station and the avionics system. Extreme situations such as this may make the system unsuitable for some users. The user may need to make bandwidth compromises or modify the system to account to suit their individual needs.

##### 1.3.4.2 Safety Considerations

**Remote Launch Capabilities:** As avionics system will be capable of remote launch capabilities, the user will be able to wirelessly ignite the rocket motor from mission control. However, premature ignition of the rocket is an important safety consideration when designing a system with these capabilities. Therefore, the system must be designed with care to ensure there is a very low risk of premature ignition of the rocket motor. The system must have extensive documentation regarding the processes to follow when operating the remote launch system. Furthermore the system must be designed to minimise the risk of injury even if the system is operated incorrectly.

-------

## 2. References

References to other documents or standards. Follow the IEEE Citation  Reference scheme, available from the [IEEE website](https://www.ieee.org/) (please use the search box). (1 page, longer if required)

[1]  Civil Aviation Authority New Zealand, “Intro to Part 101 rules for unmanned aircraft,” May 2020. [Online]. Available: https://www.aviation.govt.nz/drones/rules-and-regulations-for-drones-in-new-zealand/part-101-rules-for-drones/. [Accessed 21 May 2020].

[2]  Radio Spectrum Management New Zealand, “Licensing in New Zealand | Radio Spectrum Management New Zealand,” May 2020. [Online]. Available: https://www.rsm.govt.nz/licensing/licensing-in-new-zealand/. [Accessed 15 May 2020].

[3]  Estes Rockets, “Estes_Engine_Chart,” 2020. [Online]. Available: https://estesrockets.com/wp-content/uploads/Educator/Estes_Engine_Chart.pdf. [Accessed 18 May 2020].

[4]  Estes Rockets, “Estes_2016_Catalog,” 2016. [Online]. Available: https://estesrockets.com/wp-content/uploads/Catalogs/Estes_2016_Catalog.pdf. [Accessed 14 May 2020].

[5]  Wikipedia and Various, “Altitude - Wikipedia,” 13 April 2020. [Online]. Available: https://en.wikipedia.org/wiki/Altitude#Temperature_profile. [Accessed 18 May 2020].

[6]  E. Technicians, “ECS BOM Requirements,” 2015 May 4. [Online]. Available: https://ecs.wgtn.ac.nz/foswiki/pub/Support/TechNoteAltiumDesignerTrainingFiles/ECS_BOM_and_PCB_Design_Requirements.pdf. [Accessed 22 May 2020].

[7]  Aerospace Education, “For all things Rocketry - Aerospace Education,” MYOB, 2020. [Online]. Available: http://www.aerospaceeducation.co.nz/. [Accessed 22 May 2020].

[8]  K. D. Team, “Download | KiCad EDA,” May 2020. [Online]. Available: https://kicad-pcb.org/download/. [Accessed 22 May 2020].

[9]  Microsoft, “Down Visual Studio Code,” 2020. [Online]. Available: https://code.visualstudio.com/download. [Accessed 21 May 2020].

[10]  M. Hart, “TinyGPS++ | Arduiniana,” 2020. [Online]. Available: http://arduiniana.org/libraries/tinygpsplus/. [Accessed 21 May 2020].

[11]  OnShape, “Onshape | Product Development Platform,” 2020. [Online]. Available: https://www.onshape.com/. [Accessed 20 May 2020].

---

## 3. Specific requirements  

### 3.1 External interfaces

#### 3.1.1 Primary Sensory Instruments

The sensory instruments report information about the physical unit’s condition during pre-launch sequences and flight. These measurements must include either measurements for, or information that can be used to calculate the following information about the unit:

- Global position/literal position
- Real time altitude
- Extrapolated velocity
- Current axial alignment

These components are all essential for nominal operation of the unit in flight.

The measurements are sampled from the sensors during unit operation and are provided as input to the software system for processing. The software system interprets these measurements into logical reaction control system (RCS) actions.

#### 3.1.2 Black Box Storage Media

The black box unit stores information about the flight of the rocket. It will record information about inputs and outputs relating to the sensing instruments, trajectory controls, as well as the ground team communication interface. Essentially, it should keep track of all inputs, input processing, and outputs, and record all of this information to some digital storage media.  

The black box recording device will accept input from the software system, to be recorded. This will consist of all raw inputs from other components, all processed data from other components, and all outputs being sent to other components. It will then write all of this data to a designated onboard storage medium, in a format that can be read easily later.

#### 3.1.3 Trajectory Controls

The rocket is to be propelled by a solid fuel rocket engine. As it stands, a fixed engine causes a rocket to become unstable during an extended flight time; in fact, the system may exhibit positive feedback, as the engine could further propel the rocket off-course. As such, the system requires control for the trajectory.

Commonly, this may be either a gimbal type system for manipulating the thrust from the solid fuel engine, or manipulatable external fins. Either way, the system will need some sort of motor outputs, which would be controlled by the system’s control board. Data related to the necessary adjustments would be collected by sensory instruments; the most notable data being axial position/alignment.

#### 3.1.4 Ground Team Communication Interface

While telemetric data collected by the system should be stored on board, some (or all) of the data should also be relayed to a ground control team in real time. Physically, a radio transmitter-receiver pair will be necessary.

A specific format for the telemetric data will have to be agreed upon between the systems and “mission control” teams. It is expected that the receiving side of the radio interface will use a standard serial interface. The control board for the rocket system will handle packaging and sending data through the transmission subsystem/module, taking the data from the sensory instruments.

### 3.2 Functions

#### 3.2.1 Use Case Diagram

```plantuml
@startuml
skinparam usecase {
  BackgroundColor<< Important >> GreenYellow
  BorderColor<< Important >> Black
}

actor "Rocket Technician" as rocket_technician
actor "Mission Control Staff" as mission_control_guy
actor "Tester" as tester
actor "Team Member" as team_member

package Mission_Control {
  usecase "Collect Data from Base Station" as collect_data_from_base_station
}

package Base_Station {
  usecase "Collect Data from Rocket" as collect_data_from_rocket
  usecase "Send Data to Mission Control" as send_data_to_mission_control
}

package Rocket {

  usecase "Parachute Check"  << Important >> as parachute_check
  usecase "Install Motor" as install_motor
  usecase "Connecting Battery" as connecting_battery

  usecase "Remote System Power" as remote_system_power
  usecase "System Initialisation" as system_initialisation
  usecase "Initial Testing Sequence" << Important >> as initial_testing_sequence
  usecase "Measure Battery Voltage" as measure_battery_voltage
  usecase "GPS Initialisation Test" as gps_initialisation_test
  usecase "Barometer Test" as barometer_test
  usecase "Temperature Test" as temperature_test
  usecase "Accelerometer Calibration" as accelerometer_calibration
  usecase "Radio Link Test" as radio_link_test
  usecase "Sending Test Data to Base Station" as test_data_to_base_station

  usecase "Remote Launch" as remote_launch
  usecase "Remote Shutdown" << Important >> as remote_shutdown
  usecase "Launching Sequence" <<Important>> as launching_sequence
  usecase "Shut Down" as shut_down
  usecase "Motor Ignition" as motor_ignition
  usecase "Collecting GPS Data"  << Important >> as collecting_gps_data
  usecase "Collecting Accelerometer Data" as collecting_accelerometer_data
  usecase "Collecting Barometer Data" as collecting_barometer_data

  usecase "Processing Current Data" as processing_current_data
  usecase "Export Data to Storage"  << Important >> as export_data_to_storage
  usecase "Send Data to Base Station" << Important >> as send_data_to_base_station
  usecase "Compute new gimbal position" as compute_new_gimbal_position
  usecase "Adjust Gimbal" as adjust_gimbal
  usecase "Check Accelerometer Data for Apex" as check_accelerometer_data_for_apex
  usecase "Release Hardware Locks" as release_hardware_locks
  usecase "Release Parachute" << Important >> as release_parachute
  usecase "Send GPS Data to Base Station" as send_gps_data_to_base_station
  usecase "Check Accelerometer for no speed"  << Important >> as check_accelerometer_for_no_speed
  usecase "Activate Constant Buzzer" as activate_constant_buzzer
  usecase "Press Physical Button" as press_physical_button
  usecase "Deactivate Buzzer" as deactivate_buzzer

  usecase "Update PID Controller Variables" << Important >> as update_pid_controller_variables
}

rocket_technician --> parachute_check
rocket_technician --> install_motor
rocket_technician --> connecting_battery

mission_control_guy --> remote_system_power
remote_system_power --> system_initialisation
system_initialisation --> initial_testing_sequence
initial_testing_sequence --> measure_battery_voltage
initial_testing_sequence --> gps_initialisation_test
initial_testing_sequence --> accelerometer_calibration
initial_testing_sequence --> radio_link_test
initial_testing_sequence --> test_data_to_base_station
initial_testing_sequence --> barometer_test
initial_testing_sequence --> temperature_test

mission_control_guy --> remote_launch
mission_control_guy --> remote_shutdown
tester --> remote_launch
tester --> remote_shutdown
remote_shutdown .> shut_down : "If in Launching Sequence"
remote_launch --> launching_sequence
launching_sequence --> shut_down : "If Fail or Mission Control Shutdown"
launching_sequence --> motor_ignition : "If Success"
motor_ignition  --> collecting_gps_data
motor_ignition --> collecting_accelerometer_data
motor_ignition --> collecting_barometer_data

collecting_gps_data --> processing_current_data
collecting_accelerometer_data --> processing_current_data
collecting_barometer_data --> processing_current_data

processing_current_data --> export_data_to_storage

processing_current_data --> send_data_to_base_station
send_data_to_base_station --> collect_data_from_rocket
collect_data_from_rocket --> send_data_to_mission_control
send_data_to_mission_control --> collect_data_from_base_station

processing_current_data --> compute_new_gimbal_position
compute_new_gimbal_position --> adjust_gimbal

processing_current_data --> check_accelerometer_data_for_apex
check_accelerometer_data_for_apex --> release_hardware_locks
release_hardware_locks --> release_parachute
release_parachute --> send_gps_data_to_base_station
send_gps_data_to_base_station --> check_accelerometer_for_no_speed
check_accelerometer_for_no_speed --> activate_constant_buzzer

team_member --> press_physical_button
press_physical_button --> deactivate_buzzer

tester --> update_pid_controller_variables
@enduml
```

#### 3.2.2 Launching Sequence

**What is the Goal of the use case?**  
The goal of the "Launch Sequence" use case is to ensure the rocket is ready to launch before it actually launches.

**Who benefits from the result of this use case?**  
Everyone who has worked on the rocket would benefit from this use case as it reduces the chance of an error occurring before launch.
The people who would most benefit from this would be the Mission Control staff that would be monitoring the launch.
This is because it allows them to check any issues before the ignition, and know with confidence that nothing unexpected will happen without their input.

**How will this use case be achieved?**  
This use case will be achieved through implementing some sort of countdown with several user confirmations via mission control to ensure everything is in check before ignition. This includes verifying all sensory data is nominal, and the GPS system has acquired a signal.

**How will we judge/measure that this use case has been taken into account?**  
We can ensure that this use case has been taken into account if the launch sequence occurs when the "remote launch" button has been pressed by Mission Control.

**What limitations are there to achieving the use case?**  

- This requires some sort of input from Mission Control, hence some integration with them to allow to send/receive data needs to be developed. This may take the form of an API that is agreed upon by this group and mission control.
- The launching sequence will also need to test every functionality of the rocket before being ready to launch, hence the completion of the launch sequence will only happen once every other aspect of the rocket has been finalised.

#### 3.2.3 Initial Testing Sequence

**What is the Goal of the use case?**  
The goal of the "Initial Testing Sequence" use case is to ensure that the rocket functionality works when the system is powered on.
For clarification, this is different to the launching sequence, since this is an "automated" process, rather than the manual process from the "Launch Sequence" use case.

**Who benefits from the result of this use case?**  
This use case benefits the Rocket Technicians the most, since it allows them to immediately know if anything is wrong with the system without the need to go through a test or an actual launch.

**How will this use case be achieved?**  
This use case will be achieved through having the system automatically go into this test sequence once the system initialises itself.

**How will we judge/measure that this use case has been taken into account?**  
We can judge that this use case has been taken to account if the initial test sequence runs on system initialisation.

**What limitations are there to achieving the use case?**  
The main limitation to this use case being implemented is that all the other functions of the rocket (eg. GPS data collection, barometer data collection, data processing) needs to be functioning correctly.

#### 3.2.4 Remote Shutdown

**What is the Goal of the use case?**  
The goal of the "Remote Shutdown" use case is to be able to stop the launch of the rocket before the "actual launch" of the rocket.

**Who benefits from the result of this use case?**  
Mission Control and any Rocket Testers of the system would benefit from the remote shutdown, since it gives them more control of the rocket. More control over the rocket is better for everyone, especially due to the volatility of engines. This will increase the safety factor associated with the rocket launch.

**How will this use case be achieved?**  
This use case will be achieved by allowing Mission Control or any Testers to be able to shutdown the system at any stage of the Launch Sequence. Within this stage, there will be several user prompts (see Use Case: Launch Sequence) which gives plenty of intervals for a check to occur if the "Remote Shutdown" has occurred.

**How will we judge/measure that this use case has been taken into account?**  
We can measure if this Use Case works as expected through the following process:

- Remove the ignition and the engine, so no premature ignitions can occur.
- At every possible stage during the Launch Sequence, attempt to shutdown the system remotely.
- If it does not shutdown during any phase of the Launch Sequence, then the system has failed. Conversely, if it shuts down at every possible stage, then the use case has been successfully taken into account.

**What limitations are there to achieving the use case?**  

- The launch sequence needs to be implemented before this use case can be tested/implemented.
  - The launch sequence also has its own dependencies, therefore the use case can only be implemented at the very end stages.

#### 3.2.5 Collecting GPS Data

**What is the Goal of the use case?**  
The goal of the "Collecting the GPS Data" use case is to collect the GPS data from the rocket during launch, or during test launches.

**Who benefits from the result of this use case?**  
This benefits the Mission Control staff, as well as any team member that will be tasked with retrieving the rocket. This helps the Mission Control staff since it allows them to be able to record and use this information. This use case helps the "rocket retrievers" find where the rocket is, as the GPS data will give an approximate location. It should be noted that this benefit is only realised if the use case "Send Data to Base Station", and all the use cases on that branch, are all working as intended.

**How will this use case be achieved?**  
This use case will be achieved by the GPS unit in the rocket send its data over to the microcontroller to process it. The micro controller will then need to send this data to the radio transceiver.

**How will we judge/measure that this use case has been taken into account?**  
We can judge if this use case has been taken into account only in conjunction with the use cases: "Processing Current Data" and "Export Data to Storage". If accurate GPS data is recorded on the storage, then we can make the assumption that the collection of GPS data has been a success.

**What limitations are there to achieving the use case?**  

- The physical GPS unit needs to be with the system builders, as different GPSs may provide different outputs that need to be accounted for.
- The expected location data needs to be retrieved from a known and accurate external source to compare with data obtained from tests.
- The system must be tested outdoors, with no geographical obstructions in order to obtain a GPS signal.

#### 3.2.6 Send Data to Base Station  

**What is the Goal of the use case?**  
The goal of the "Send Data to Base Station" use case is to send the processed and collated data from the rocket to the base station.

**Who benefits from the result of this use case?**  
The use case benefits only the Mission control staff, since the data will also be exported elsewhere (such as the rocket local storage).

**How will this use case be achieved?**  
This use case will be achieved through the use of the radio transmitter, which would transmit the data to the base station on a specific frequency.

**How will we judge/measure that this use case has been taken into account?**  

- We can judge if this use case works if the base station receives data from the rocket (testing in conjunction with use case "Receiving Data From Rocket"). This data must be received and be interpreted correctly, as it would show that the data has been transmitted correctly, even through possible interferences.
- The testing must also take into account interferences as this would better reflect the actual conditions that the rocket would be in.
  - This would mean that we need to test using walls, moving obstructions (such as people), and create other signals (like mobile calls and internet usage) while testing.

**What limitations are there to achieving the use case?**  

- The limitations of achieving this use case is that we would have to test this in conjunction of the "Receiving Data From Rocket" use case. This may create the issue that it would not always be clear on which part of the process is failing.
- The test will also need to take place outdoors to accurately reflect a rocket launch scenario

#### 3.2.7 Writing Data to Storage  

**What is the Goal of the use case?**  
The goal of the writing data to storage use case is to store the logging data on physical media onboard the rocket at all times.

**Who benefits from the result of this use case?**  
This benefits the Testers and Programmers of the avionics package as they will be able to review all data and logging after a flight has occurred. As wireless transmissions have a bandwidth cap and are potentially lossy, it is beneficial to store the logging data with 100% accuracy. This will allow us to see all readings from all instruments in file form after a flight has occurred. Additionally, in the event of a catastrophic failure, this may allow for analysis of what caused the failure.

**How will this use case be achieved?**  
This use case will be achieved through the reading of the instruments in real time and writing the readings and logs to the physical media, eg an SD card by the microcontroller.

**How will we judge/measure that this use case has been taken into account?**  
We check that this use case has been taken into account by being able to read the files recorded by the data recorder on another device after a flight, irrespective of flight outcome.

**What limitations are there to achieving the use case?**  

- The amount of information that the microcontroller can process each cycle may limit our chances of achieving success of this use case.
- The physical media needs to survive flight in order for logging data to be retrieved.

#### 3.2.8 Processing Current Data  

**What is the Goal of the use case?**  
The goal of the Processing Current Data use case is to process the data measurements, inputs and other signals into relevant outputs. This would be done by the microcontroller in the avionics system.

**Who benefits from the result of this use case?**  
Mission control operators benefit from the information processing as it allows them to see the rocket's flight information. The Testers also benefit from the processing of information as it's a prerequisite to the data being stored on physical media onboard the rocket, for later use in analysis and debugging. Additionally, the processing of data is essential for the operation of the active control system in the rocket.

**How will this use case be achieved?**  
This use case will be achieved through the use of the microcontroller to process the input signals from the sensors in the avionics package.

**How will we judge/measure that this use case has been taken into account?**  
We can look at other use cases' success to judge whether this has been taken into account, such as successful gimbal adjustment, and exporting to data to storage. If these other use cases are deemed successful, we can make the assumption that this use case has been successful as well.

**What limitations are there to achieving the use case?**  

- Processing power of the microcontroller in the avionics package.
- Interference with the signals before they reach the microcontroller.

#### 3.2.9 Compute New Gimbal Position  

**What is the Goal of the use case?**  
The goal of the "Compute New Gimbal Position" use case is to adjust the gimbal as a result of instrumentation readings interpreted by the microcontroller.

**Who benefits from the result of this use case?**  
Everybody involved with the launch of the rocket benefits, as it is important overall for the rocket to fly in the correct and predicted trajectory.

**How will this use case be achieved?**  
This use case will be achieved through the processing and control software calculating the angle adjustments required. These values will be used by the "Adjust Gimbal" use case to change the motors direction.

**How will we judge/measure that this use case has been taken into account?**  
We will be able to see the rocket follows the correct trajectory when it flies. Also, the telemetry collected during the rocket flight should indicate that the rocket has followed the intended path.

**What limitations are there to achieving the use case?**  

- All onboard sensors functioning correctly, with no interference.
- PID values are set accurately.
- The gimbal motors function reliably.

#### 3.2.10 Release Parachute  

**What is the Goal of the use case?**  
The goal of the "Release Parachute" use case is to release the parachute and slow down the descent of the rocket. This is done to avoid any damage to the rocket, as well as anything in the path of the rocket.

**Who benefits from the result of this use case?**  
The benefits is for everyone working on the rocket, as it avoids the loss of progress on the hardware side, while also ensuring the safety of everyone at the launch site. This also benefits others not directly involved in the launch as it prevents them from being injured by the rocket.

**How will this use case be achieved?**  
This use case would be achieved by the parachute being released from the rocket when told to do so. This would require having a proper check to know when the rocket is falling. This can be done by measuring the velocity of the rocket while it is flying. When the velocity decreases and begins to increase again, this would signal that the rocket has reached its apex of the flight, and is beginning to fall.

**How will we judge/measure that this use case has been taken into account?**  

- We can judge this use case is taken to account if the parachute is able to be released.
- We can ensure that the parachute is being released at the right time when the velocity of the rocket decreases and begins to increase again. At this point, the parachute should have been launched. If not, then we know that the release of the parachute has failed.
- We can be further ensure the parachute releases at the correct time by using barometer readings to show us when the rocket is starting to fall.

**What limitations are there to achieving the use case?**  

- This use case can only be achieved once the parachute and the nose cone has been installed (use case "Release Hardware Lock").
- Furthermore, if the use case "Check Accelerometer Data for Apex" is not implemented yet, then some code will need to be developed to test it in isolation.
- This system can only be properly tested in an actual launch of the rocket system

#### 3.2.11 Check Accelerometer for No Speed  

**What is the Goal of the use case?**  
The goal of the "Check Accelerometer for No Speed" use case is to check for lack of speed/velocity, therefore determining that the rocket is now landed, and needs to be picked up.

**Who benefits from the result of this use case?**  
The team members out on the launch site would benefit from this the most, as this check would then allow the buzzer to turn on. This buzzer in conjunction with the GPS data would allow for the quicker retrieval of the rocket post landing. Furthermore, if the rocket GPS data fails to transmit, this would be used as a failsafe to ensure the rocket can still be found.

**How will this use case be achieved?**  
This can be achieved by the microcontroller collecting the acceleration data throughout the launch, and therefore determining the rocket velocity. When the rocket velocity reaches zero, it will be able to pass on the message to other parts of the software to perform actions such as sounding the buzzer.

**How will we judge/measure that this use case has been taken into account?**  
This use case would be judged by whether the call is made when the rocket velocity is zero. This can be done by applying test data into the MCU, and analysing the reaction of the system when this case occurs.

**What limitations are there to achieving the use case?**  
The limitation of this use case would be that there would need to exist some way to input "launch" data into the system to test these circumstances.

#### 3.2.12 Check Parachute  

**What is the Goal of the use case?**  
The goal of the "Check Parachute" use case is to ensure that the parachute is ready to be released correctly when required by the avionics system.

**Who benefits from the result of this use case?**  
This check benefits everyone involved with the rocket, but especially the testers.

- It is a benefit to everyone, since if this check is not performed, then the launch could fail, and therefore inhibiting the progress on the development and management of the rocket.
- It is especially relevant to the testers, as they would not be able to test the parachute release functionality with a proper degree of certainty if the parachute does not work.

**How will this use case be achieved?**  
This use case will be achieved by a Rocket Technician checking the rocket whenever a launch (real or test) is about to occur.

**How will we judge/measure that this use case has been taken into account?**  
We can judge that this use case has been taken into account when it is performed before a launch or a parachute release test.

**What limitations are there to achieving the use case?**  
This use case will only be able to be tested given that the parachute and rocket head are constructed and are installed in the rocket.

#### 3.2.13 Updating PID Controller Variables  

**What is the Goal of the use case?**  
The goal of the "Updating PID Controller Variables" use case is update the PID controller variables, such that when the rocket is launched, the gimbal will act appropriately with the given inputs from the flight. These values should be obtained from simulations of the rocket launch.

**Who benefits from the result of this use case?**  
This check benefits everyone involved with the rocket, but especially the Rocket Technicians.

- It is a benefit to everyone, since if the rocket does not flight straight, it is unlikely that the rocket will have a successful launch.
- It is especially relevant to the Rocket Technicians, as being unable to adjust these values would disallow the chance for accurate gimbal adjustments.

**How will this use case be achieved?**  
This use case will be achieved by a Rocket Technician adjusting the variables of the PID controller in the software.

**How will we judge/measure that this use case has been taken into account?**  
We can judge whether the use case has been taken into account on whether it is accessible for the Rocket Technician adjusting the variables of the PID controller in the software.

**What limitations are there to achieving the use case?**  

- This use case requires the implementation of the PID Controller to be completed.
- The hardware must be functioning correctly. The onboard sensors must collect accurate data, and relay this to the microcontroller with minimal interference.

### 3.3 Usability Requirements

We need to consider these requirements through all the different scenarios:

- Pre-Launch Operations
- Launch
- Flight
- Retrieval

In order to properly assess the usability requirements, we have three metrics to assess our unit by. These are:

- Measurable Effectiveness, the ability of the unit to perform tasks to a quantifiable standard
- Efficiency, the ability of the unit to perform tasks without operational inefficiencies
- Satisfaction Criteria, qualitative standards that the unit must meet

For each of our use case scenarios, we can apply these three metrics to determine whether the unit meets the usability requirements.

**Pre-Launch Operations:** During Pre-Launch Operations, the unit is preparing to launch.

*Measurable Effectiveness:* For the unit to be considered effective, it must reach the launch phase without any issues. The following operations must be nominally performed, otherwise the launch process will be aborted.

- Hardware validation, including but not limited to: Sensor and input verification.
- Software state validation.
- Clearance from the Launch Director.

*Efficiency:* For the unit to be considered efficient during Pre-Launch Operations, the unit should complete checking in a sufficient time frame. This is essential as often only a small window is allocated for launch.

*Satisfaction Criteria:* The unit checks that launch requirements are satisfied, and moves into the Launch phase as expected without error.

**Launch:** We are defining the launch process as all of the time between first ignition of the propellant, and the rocket leaving the ground.

*Measurable Effectiveness:* In order for the unit to be effective in the launch phase, the rocket must release on its intended trajectory, with little to no measurable deviation.

*Efficiency:* The unit must conserve as much propellant as possible while still allowing the unit to launch effectively.

*Satisfaction Criteria:* The unit must initiate lift off, and transition into the flight phase as outlined in flight parameters with no additional interfacing by flight operators. The complete automation of this phase is essential.

**Flight:** Flight encompasses all the time the unit spends airborne. This includes all time from the initial launch to unit touchdown.

*Measurable effectiveness:* The unit should not deviate from its intended course, with real-time corrections made to the flight path in the event that external factors influence the unit’s trajectory. Once conditions demand it, a parachute should deploy to decrease the unit's velocity. During descent, the unit should remain intact and functional.

*Efficiency:* The unit should burn the optimal amount of propellant required to keep to the expected trajectory.

*Satisfaction Criteria:* The unit must follow its intended flight course, deploy the descent parachute, and make it to landing without any functional failure, or physical damage.

**Retrieval:** The retrieval phase is entered when the unit lands after flight, during this phase the unit should be retrieved by a flight operator for potential reuse in the future.

*Measurable Effectiveness:* The unit should land in a state that allows potential reuse in the future. Importantly, data must be undamaged by any potential impact.

*Efficiency:* The unit should have a sufficiently low power usage that it can be located using a GPS signal for a sufficient amount of time afterwards.

*Satisfaction Criteria:* The unit survives landing can be located, accounting for issues, by launch operators.

### 3.4 Performance requirements

To function correctly as expected by the customer, the rocket must perform to a certain standard. These performance requirements outline what the minimum expectations of the rocket are both physically and in software.

As the rocket is a real-time safety critical system, it must be able to react to measurement changes in effective real time; this is essential for the rocket to keep functioning nominally through all stages of flight. If the processing of measurement data is poor or slow, the rocket may not react fast enough to time sensitive events, e.g. sensory data being used for guidance control. This could lead to a minor, or catastrophic, failure of the rocket system. For a rocket control system to be suitable, it must efficiently process time-critical tasks and information.

The avionics should be able to perform without error through all stages of flight, withstanding the potentially changing forces, vibrations and potentially impacts. A model rocket typically experiences an acceleration of up to 10G during launch, so the avionics system needs to be designed to withstand such forces. Furthermore, at high altitudes the air temperature decreases at a rate of 9.8°C per kilometre; thus the avionics system must be designed to withstand low temperatures without failure. This may include considering different integrated circuit packages to suit low temperature environments.

To transmit telemetry data for the purpose of analysis and monitoring, the rocket shall be fitted with a wireless transmission system capable of data transmission through all the stages of flight. The system must have sufficient range for stable data transmission from the launch site altitude to apogee altitude. The transmission range must also be capable of reaching from the launch site to the location where the rocket lands under parachute, in order to transmit the GPS data so it can be found again. This range may vary because of wind conditions and the results of the rocket's flight performance, which will differ from flight to flight.

The bandwidth capacity of the radio telemetry system should be sufficient to transmit logging data from the rocket during flight to a receiving device such as a laptop. This data would be critical for failure analysis in the event of a failure that results in the loss of the rocket for any reason. Additionally, the avionics system must have an onboard storage system that can record data from the onboard sensors at the maximum possible data rate, to ensure useful telemetric data is obtained.

The software should be able to handle and continue even with unexpected and/or faulty readings coming from the various sensors during flight. Error checking and redundancy must be in place to ensure the safety systems are able to perform correctly.

### 3.5 Logical database requirements

```plantuml
@startuml
package AvionicsSystem{

  class MicrocontrollerInterface {

  }

  class BlackBoxWriter{
  }

  class GpsModule{
  }

  class MissionControlTransceiver{
  }

  package FlightSensors{
  interface FlightControlSensor

  class FlightSensorOne implements FlightControlSensor{
  }

  class FlightSensorTwo implements FlightControlSensor{
  }

  class FlightSensorN implements FlightControlSensor{
  }
  }
  BlackBoxWriter --> MicrocontrollerInterface
  GpsModule --> MicrocontrollerInterface
  MissionControlTransceiver <--> MicrocontrollerInterface
  FlightSensorOne --> MicrocontrollerInterface
  FlightSensorTwo --> MicrocontrollerInterface
  FlightSensorN --> MicrocontrollerInterface
}
@enduml
```

#### Microcontroller Interface  

The Microcontroller Interface describes the core loop of the system and delegates most of the active tasks of the software system. It manages important events, such carrying out pre-launch system checks, as well as managing sequenced/regular events, such as data processing. The Microcontroller Interface is also responsible for polling all the sensor modules, and handles incoming data from those sensors, allowing course adjustments and data transmission back to mission control.

**Performs the Following:**  

- Run a constant time-linked loop, performing important events (eg. recording GPS data) at intervals
- Accept/request input from different sensors in the system
- Process input to determine commands for thrust control system
- Dispatch commands to thrust control system
- Handle commands from mission control, passed from the transceiver
- Handle any other incidental events

#### Black Box Writer  

The Black Box Writer class handles the writing to the avionics unit's "black box". The black box is a digital storage device that records all of the data relevant to each of the rocket's flights. This includes all inputs, outputs and processing going through the software system, as well as any error cases and logs. This class is passed data from other parts of the software system, to be formatted and recorded onto the digital storage device.

**Performs the Following:**  

- Accept packets asynchronously from other parts of the system
- Record the type and values of each packet, along with a system timestamp (eg, raw input from Sensor A with a value of 145.2)
- Save and output the data streams into their separate, respective files under a separate directory for each launch.

#### GPS Module  

The GPS Module class handles the action of receiving input from the GPS unit. Once it receives information from the GPS unit, it then reports that information back to the rest of the system to be sent to mission control via the transceiver. Since this information is not used for controlling the rocket while it is in flight, it should be handled separately from the flight control inputs.

**Performs the Following:**  

- Accept GPS location data from the hardware module
- Report this data to the rest of the software system

#### Mission Control Transceiver  

The Mission Control Transceiver class handles the actions of sending and receiving commands from mission control. The class would receive commands transmitted from mission control, and redirect it to the avionics system to be interpreted appropriately. Additionally, the class will also package and then transmit the data passed from the microcontroller interface back to mission control system.

**Performs the Following:**  

- Receive incoming command messages in a predetermined format from mission control
- Pass interpreted messages to the rest of the software system
- Accept messages to be transmitted to mission control, from the rest of the system
- Package and transmit the messages to mission control

#### Flight Control Sensors  

This is an interface for handling inputs from the rocket's various sensors while the rocket is in flight. It will convert the raw signals received from hardware components, and present sanitised inputs to the rest of the software system. Depending on the specific sensors used, there may be any number of implementations of this interface (one for each sensor).

**Performs the Following:**  

- Accept raw input from the sensor
- Transform raw input into workable data
- Sanitise the workable data to be safe.
- Report the sanitised workable data to the microcontroller interface.

### 3.6 Design constraints

The design constraints define limits, standards and specifications that the unit's software and hardware systems must adhere to. These constraints can be customer requirements, external standards, regulatory requirements or project limitations.

**Physical Properties of Rocket:**  
The rocket must adhere to the Civil Aviation Authority (CAA) regulations for model rockets, specifically Part 101 rules for unmanned aircraft. The regulations can be found at https://www.aviation.govt.nz/assets/rules/consolidations/Part_101_Consolidation.pdf.

The rocket must adhere to the following regulations:

- The rocket must weigh less than 1.5kg.
- The rocket's body components must be constructed of lightweight, non-metal parts.
- The rocket must use less than 125 grams of propellent.
- The rocket must use certified, commercially made rocket motors that have not been modified.
- The rocket must not produce more than 320 Newton seconds of impulse.
- The rocket must use a slow burning propellant.
- The rocket must be launched outdoors in ideal weather.
- The rocket must be launched remotely.

Both the CAA regulations and the customer require the rocket use a common type of rocket motor.

**Budget:** The rocket must be able to be produced within the limited budget provided.

**Reusability:** The customer expects that the rocket is able to be reused at least 10 times. This requires that the rocket uses parachutes to land safely, which are deployed at apogee. The rocket thus should be designed to withstand the forces, vibrations and potentially impacts of Launch, Flight and Landing with none or minimal damage.

The NZ Rocketry Association also state in their safety guidelines that a recovery system, such as a parachute, must be used so that the rocket safely returns to the ground.

**Open Source:** The software avionics package produced for the rocket must be released and licensed as open source for use by other members of the model rocket community. Hence, all dependencies must be open source, and the avionics package must adhere to all rules under their respective license(s) defined by the other open source dependencies used, if any.

**Radio Communication Systems:** All radio communication systems in the rocket must adhere to the relevant regulation including the Radiocommunications Act 1989 and the Radiocommunications Regulations 2001. The rocket must use a freely available frequency for communication to the base station. For the data to be relayed reliably the system shall operate on a frequency that has the least interference.

Relevant regulation and guidelines can be found through the following links:

- https://www.rsm.govt.nz/licensing/licensing-in-new-zealand/
- http://www.legislation.govt.nz/act/public/1989/0148/latest/DLM195576.html
- http://www.legislation.govt.nz/regulation/public/2001/0240/latest/DLM71513.html

### 3.7 Nonfunctional System Attributes

***The following are the relevant systemic requirements of the product:***  

- Time Behaviour
- Ease of Use
- Scalability for Distribution
- Withstanding flight and touchdown
- Recoverability
- Reusability
- Weight Constraints
- Testing
- Maintenance
- Motor and Propellant

**Time Behaviour:**  
The launch is the time critical phase of the rockets use. GPS information must be transmitted and the motor gimbal adjusted continuously throughout the flight, and the parachute must deploy as soon as the rocket descends. For this to be accomplished the avionics system will need to handle these simultaneous tasks without a queue of tasks building up. To ensure the most important events are prioritised, hardware interrupts may need to be implemented.

**Ease of Use:**  
Launching the rocket should be a streamlined process. Physical setup should consist of filling the propellant with minimal disassembly of the rocket before mounting the rocket on a launch pad. Specific instructions will be included for packing the parachute. Software set up should consist of a remote mission control system requesting access after a physical switch was been turned on. To assist in the ease of use, accurate and detailed supporting documentation needs to be produced.

**Scalability for Distribution:**  
Gimbal control should be able to scale up to larger rockets and motors with tuning. Additionally, system design should be well enough documented that it is reproducible by another team with no relation to development team. Furthermore, activities such as the process of tuning PID parameters should be documented to allow other user to apply this system to their application.

**Withstanding flight and touchdown:**  
All components used in flight must be able to function for the whole duration of the flight. To maintain the integrity of the rocket, the parachute must be reliably able to deploy after the rocket has reached the apex of its flight. Sensory and software components must survive touchdown, so that the rocket can be reused. Ensuring the black box data remains safe in the event of a failure is particularly important to ensure that the cause of the failure can be found. This may involve extra physical protections for the black box component of the system.

**Recoverability:**  
In the event of encountering an error pre-launch the rocket must enter an error state where it cannot launch. This error state will contain an error log so the issue can be reviewed. Any errors encountered in-flight should shut off the motor and deploy the parachute to avoid the rocket taking an unpredictable trajectory.

**Reusability:**  
The rocket must be able to be reused after a launch. This will require that the parachute system is able to safely return the rocket to the ground. The parachute and propellant will need to be replaced and the avionics system will need to be reset.

**Weight Constraints:**  
In order to be considered a model rocket the rocket must weigh less than 1.5kg (according to the NZ Rocketry Association). The weight is further restricted by the fact that Class C and D motors will be used, which allow a maximum weight of around 300g.

**Testing:**  
All states of the avionics system are to be tested that it can establish communications with mission control, enter error states safely, the gimbal control reacts safely, and that the parachute deploys reliably. This will ensure the safety of the user and people and object in the launch environment of the rocket.

**Maintenance:**  
The motor must be easily accessible and removable. All moving components must be checked for damage and cleaned before and after testing. The Parachute must be checked of tears and the strings checked for fraying. Additionally, the electrical connections between the components must be checked to ensure the avionics system will operate correctly.

**Motor and Propellant:**  
The rocket will not contain more than 125 grams of propellant nor produce more than 320 N-secs of total impulse in accordance with the NZ Rocketry Association.

**Open Source:**  
All dependant systems that are used in this project must be open source. This avionics package must meet the requirements of the open source licence.
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

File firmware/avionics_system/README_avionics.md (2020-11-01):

# README for the Avionics System

## Avionics System Platform

The Avionic System was developed on the [**PlatformIO**](https://platformio.org/) platform, with the STM32F405 Chip.

## What does the System do?

This system does not perform what we had originally set out to do for our minimum viable product. There were several issues that had occured during the development of the rocket, in particular the delays in hardware testing, and software integration. Our software in our avionics system performs the following:

* **Has a functioning Finite State Machine (FSM)**
  * Each state of the FSM can be determined through the on-board RGB LED on the STM32F405 chip. The states include:
    * **Boot Up** - This is not explicity a state, however it sets up all proprietary requirements from the Arduino Framework such as LED capabilities. This is represented on the on-board chip with 10 Red Blinks, then 10 Green Blinks. 
    * **Initialisation** - This sets up the sensors and other components so they are active. The LED colour on the on-board chip is Orange.
    * **Test** - This performs a series of tests to make sure that the sensors are working. The LED colour on the on-board chip is Yellow. The LED will also represent each of the possible errors that can occur during the testing. These are:
      * **Battery Failure** - Cyan
      * **GPS Failure** - Mauve (Purple/Brown)
      * **Accelerometer** Failure - Chareuse (Yellow)
      * **Barometer Failure** - Teal
      * **Temperature Sensor Failure** - Russet (Brown)
      * **Radio Link Failure** - White
      * **Gimbal Failure** - Hot Pink
      * **Black Box Failure** - Glaucous (Blue)
    * **Idle** - The is when the system is ready to be launched, but is not launched yet. The LED colour on the on-board chip is Green.
    * **Launch Sequence** - This is when the system is performing the launch sequence. This state includes a countdown. The idea is that the interupts via the Radio Link can stop the countdown, and put the system into failure. The LED colour on the on-board chip is Cyan.
    * **Ignition** - This is when the system's software lock on the ignition is freed, and the rocket is available to be launched via hardware implementations. The LED colour on the on-board chip is Blue.
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

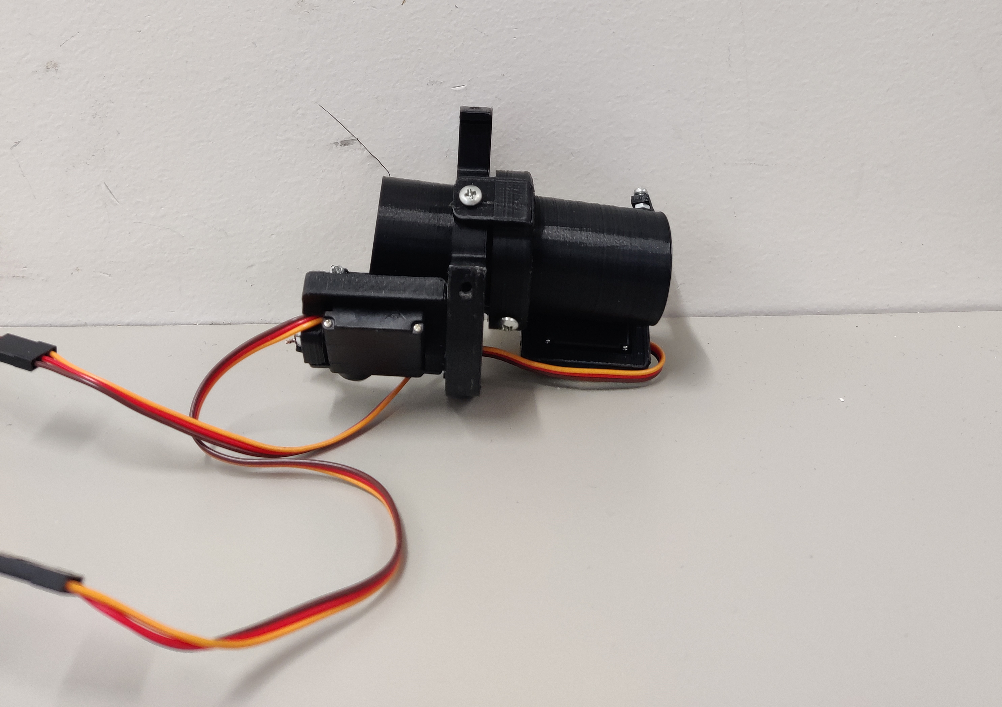
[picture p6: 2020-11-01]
hardware/3D_models/images/gimbal_2.jpg

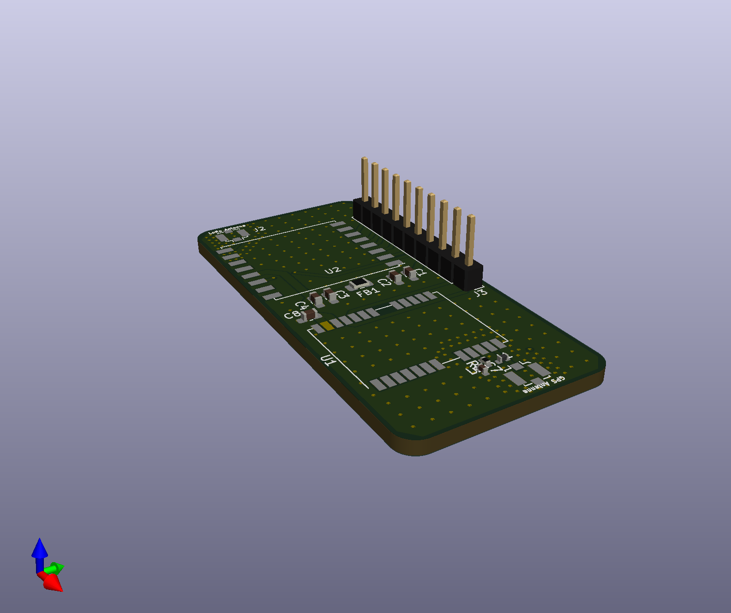
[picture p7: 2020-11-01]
hardware/avionics_system/rf_schematic_and_pcb/images/PCB_front_view.png

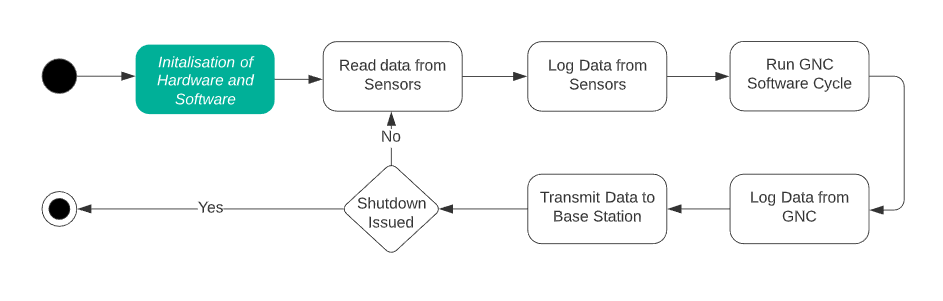
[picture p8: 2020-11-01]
documentation/architecture_design/images/activity-diagram.png

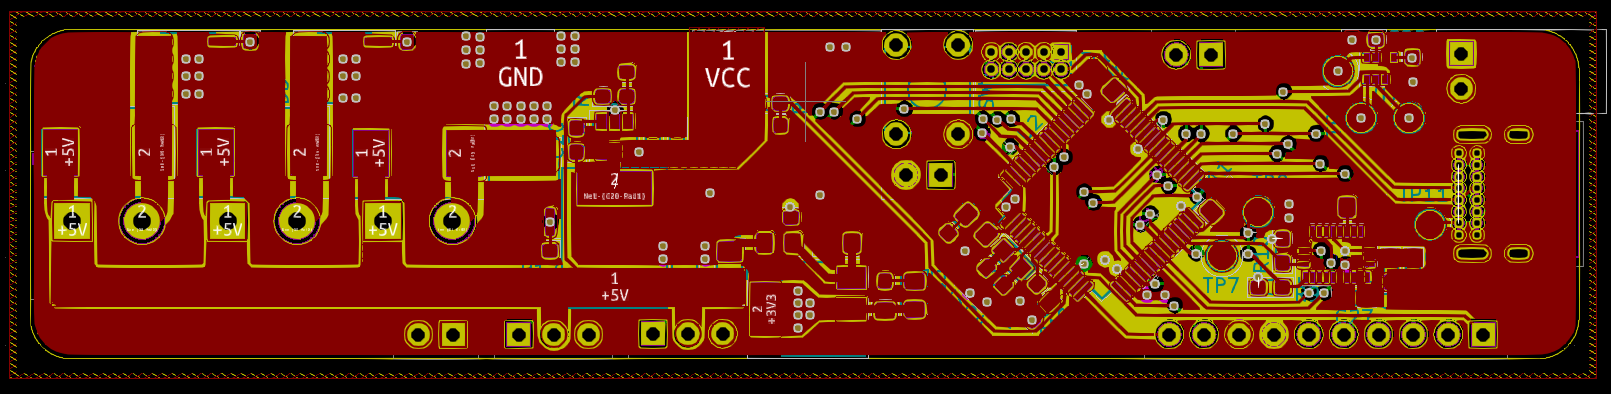
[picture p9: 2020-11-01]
hardware/avionics_system/main_board_schematic_and_pcb/images/PCB_design.png

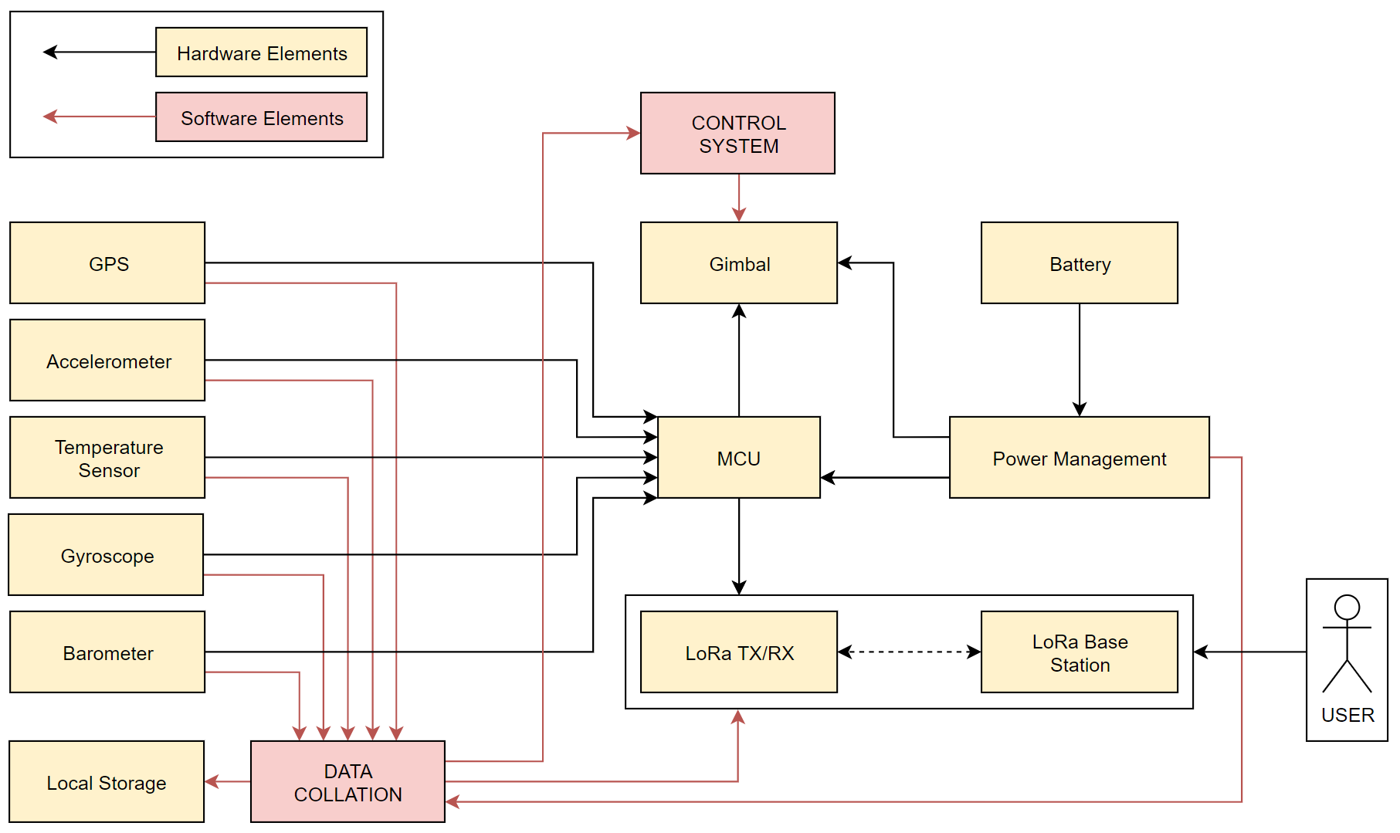
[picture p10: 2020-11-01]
documentation/architecture_design/images/4.6_diagram.png

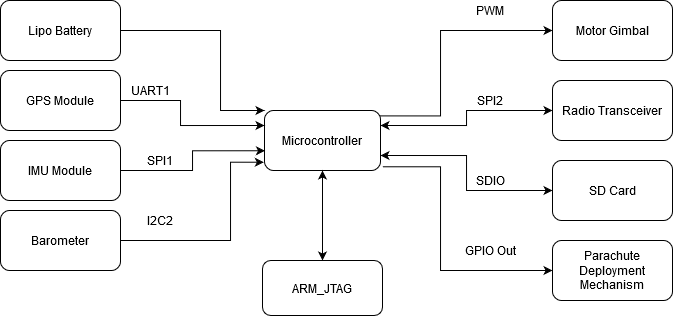
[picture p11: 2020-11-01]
documentation/architecture_design/images/avionics_system_block_diagram.png

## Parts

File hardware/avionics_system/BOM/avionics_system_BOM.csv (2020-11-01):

Source:
Date: | 24/06/2020 21:35
Tool: | Eeschema (5.1.5)-3
Generator:
Component Count:
Ref | Value | Cmp name | Footprint | Description | Vendor |  | Qnty
C1, C2, C3, C4, C6, C8, C11, C12, C14, C18, C19, C22, C23, C24, C26, C27, C28, C29, C30, | 100n | C | Capacitor_SMD:C_0603_1608Metric_Pad1.05x0.95mm_HandSolder | Unpolarized capacitor | Digi-Key | 399-1100-1-ND | 20
C5, C16, C17, C21, | 10u | C | Capacitor_SMD:C_0805_2012Metric_Pad1.15x1.40mm_HandSolder | Unpolarized capacitor | Digi-Key | 399-4925-1-ND | 4
C7, C10, | 2.2u | C | Capacitor_SMD:C_0805_2012Metric_Pad1.15x1.40mm_HandSolder | Unpolarized capacitor | Digi-Key | 311-1463-1-ND | 2
C9, | 22uf | C | Capacitor_SMD:C_0805_2012Metric_Pad1.15x1.40mm_HandSolder | Unpolarized capacitor | Digi-Key | 399-4696-1-ND | 1
C13, | 470u | C | Capacitor_SMD:CP_Elec_10x10.5 | Unpolarized capacitor | Digi-Key | 493-6386-1-ND | 1
C15, C20, C25, C31, | 10n | C | Capacitor_SMD:C_0603_1608Metric_Pad1.05x0.95mm_HandSolder | Unpolarized capacitor | Digi-Key | 399-7842-1-ND | 4
D1, | 1N5819 | 1N5819 | Diode_THT:D_DO-41_SOD81_P10.16mm_Horizontal | 40V 1A Schottky Barrier Rectifier Diode, DO-41 | Digi-Key | 497-6610-1-ND | 1
D2, D3, | LED | LED | LED_SMD:LED_0805_2012Metric_Pad1.15x1.40mm_HandSolder | Light emitting diode | Digi-Key | 475-1415-1-ND | 2
F1, | 1A | Fuse | Fuse:Fuse_1206_3216Metric_Pad1.42x1.75mm_HandSolder | Fuse | Digi-Key | SF-1206S100-2CT-ND | 3
FB1, FB2, FB5, | Ferrite_Bead_Small | Ferrite_Bead_Small | Resistor_SMD:R_0805_2012Metric_Pad1.15x1.40mm_HandSolder | Ferrite bead, small symbol | Digi-Key | 587-1903-1-ND | 3
J1, | Conn_01x01_Female | Conn_01x01_Female | TestPoint:TestPoint_Pad_D3.0mm | Generic connector, single row, 01x01, script generated (kicad-library-utils/schlib/autogen/connector/) | Digi-Key | - | 1
J2, | Conn_01x01_Female | Conn_01x01_Female | TestPoint:TestPoint_Pad_3.0x3.0mm | Generic connector, single row, 01x01, script generated (kicad-library-utils/schlib/autogen/connector/) | Digi-Key | - | 1
J3, | Conn_01x01_Female | Conn_01x01_Female | TestPoint:TestPoint_Pad_D4.0mm | Generic connector, single row, 01x01, script generated (kicad-library-utils/schlib/autogen/connector/) | Digi-Key | - | 1
J4, | Conn_01x01_Female | Conn_01x01_Female | TestPoint:TestPoint_Pad_4.0x4.0mm | Generic connector, single row, 01x01, script generated (kicad-library-utils/schlib/autogen/connector/) | Digi-Key | - | 1
J5, J13, | Conn_01x02_Female | Conn_01x02_Female | Connector_PinHeader_2.54mm:PinHeader_1x02_P2.54mm_Vertical | Generic connector, single row, 01x02, script generated (kicad-library-utils/schlib/autogen/connector/) | Digi-Key | 952-2262-ND | 2
J6, | USB_C_Receptacle_USB2.0 | USB_C_Receptacle_USB2.0 | Connector_USB:USB_C_Receptacle_GCT_USB4085 | USB 2.0-only Type-C Receptacle connector | Digi-Key | 2073-USB4085-GF-ACT-ND | 1
J7, J11, | Conn_Coaxial | Conn_Coaxial | Connector_Coaxial:U.FL_Molex_MCRF_73412-0110_Vertical | coaxial connector (BNC, SMA, SMB, SMC, Cinch/RCA, ...) | Digi-Key | WM5587CT-ND | 2
J8, | ARM_JTAG | Conn_ARM_JTAG_SWD_10 | Connector_PinHeader_1.27mm:PinHeader_2x05_P1.27mm_Vertical | Cortex Debug Connector, standard ARM Cortex-M SWD and JTAG interface | Digi-Key | 1175-1627-ND | 1
J9, J12, | Conn_01x03_Male | Conn_01x03_Male | Connector_PinHeader_2.54mm:PinHeader_1x03_P2.54mm_Vertical | Generic connector, single row, 01x03, script generated (kicad-library-utils/schlib/autogen/connector/) | Digi-Key | 732-5316-ND | 2
J10, J14, | Conn_01x02_Male | Conn_01x02_Male | Connector_PinHeader_2.54mm:PinHeader_1x02_P2.54mm_Vertical | Generic connector, single row, 01x02, script generated (kicad-library-utils/schlib/autogen/connector/) | Digi-Key | 952-2262-ND | 2
J15, J16, J17, | Conn_01x02_Female | Conn_01x02_Female | TerminalBlock_Phoenix:TerminalBlock_Phoenix_MKDS-1,5-2-5.08_1x02_P5.08mm_Horizontal | Generic connector, single row, 01x02, script generated (kicad-library-utils/schlib/autogen/connector/) | Digi-Key | 277-1247-ND | 3
J18, | Micro_SD_Card_Det | Micro_SD_Card_Det | Connector_Card:microSD_HC_Molex_104031-0811 | Micro SD Card Socket with card detection pins | Digi-Key | WM6357CT-ND | 1
L1, | 27n | L | Inductor_SMD:L_0603_1608Metric_Pad1.05x0.95mm_HandSolder | Inductor | Digi-Key | 712-1439-1-ND | 1
Q1, Q2, Q3, | IRF8721PBF-1 | IRF8721PBF-1 | Package_SO:SOIC-8_3.9x4.9mm_P1.27mm | 14A Id, 30V Vds, HEXFET N-Channel MOSFET, SO-8 | Digi-Key | IRF8721TRPBFCT-ND | 3
R1, R2, | 2.2k | R | Resistor_SMD:R_0603_1608Metric_Pad1.05x0.95mm_HandSolder | Resistor | Digi-Key | P2.2KGCT-ND | 2
R3, | 300k | R | Resistor_SMD:R_0603_1608Metric_Pad1.05x0.95mm_HandSolder | Resistor | Digi-Key | RR08P300KDCT-ND | 1
R4, | 100k | R | Resistor_SMD:R_0603_1608Metric_Pad1.05x0.95mm_HandSolder | Resistor | Digi-Key | RR08P100KDCT-ND | 1
R5, R6, R9, R10, R15, | 10k | R | Resistor_SMD:R_0603_1608Metric_Pad1.05x0.95mm_HandSolder | Resistor | Digi-Key | P10KGCT-ND | 5
R11, R12, | 5.1k | R | Resistor_SMD:R_0603_1608Metric_Pad1.05x0.95mm_HandSolder | Resistor | Digi-Key | 311-5.10KHRCT-ND | 2
R13, R14, | 4.7k | R | Resistor_SMD:R_0603_1608Metric_Pad1.05x0.95mm_HandSolder | Resistor | Digi-Key | RR08P4.7KDCT-ND | 2
R16, R17, R18, | 470 | R | Resistor_SMD:R_0603_1608Metric_Pad1.05x0.95mm_HandSolder | Resistor | Digi-Key | 311-470GRCT-ND | 3
R19, | 10 | R | Resistor_SMD:R_0603_1608Metric_Pad1.05x0.95mm_HandSolder | Resistor | Digi-Key | 311-10.0HRCT-ND | 1
SW1, | SW_Push | SW_Push | Button_Switch_THT:SW_TH_Tactile_Omron_B3F-10xx | Push button switch, generic, two pins | Digi-Key | SW402-ND | 1
TP1, TP2, TP3, TP4, TP5, TP6, TP7, TP8, TP9, TP10, TP11, TP12, TP13, | TestPoint | TestPoint | TestPoint:TestPoint_Pad_D2.0mm | test point | Digi-Key | - | 13
U1, | AMS1117-3.3 | AMS1117-3.3 | Package_TO_SOT_SMD:SOT-223-3_TabPin2 | 1A Low Dropout regulator, positive, 3.3V fixed output, SOT-223 | Digi-Key | AZ1117EH-3.3TRG1DICT-ND | 1
U2, | STM32F405RGTx | STM32F405RGTx | Package_QFP:LQFP-64_10x10mm_P0.5mm | ARM Cortex-M4 MCU, 1024KB flash, 128KB RAM, 168MHz, 1.8-3.6V, 51 GPIO, LQFP-64 | Digi-Key | 497-11767-ND | 1
U3, | AMS1117-5.0 | AMS1117-5.0 | Package_TO_SOT_SMD:SOT-223-3_TabPin2 | 1A Low Dropout regulator, positive, 5.0V fixed output, SOT-223 | Digi-Key | AZ1117EH-5.0TRG1DICT-ND | 1
U4, | NEO-M8N | NEO-M8N | RF_GPS:ublox_NEO | GNSS Module NEO M8, VCC 2.7V to 3.6V | Digi-Key | 672-NEO-M8N-0CT-ND | 1
U5, | LSM9DS1 | LSM9DS1 | Package_LGA:LGA-24L_3x3.5mm_P0.43mm | I2C SPI 9 axis IMU accelerometer gyroscope magnetometer | Digi-Key | 497-14946-1-ND | 1
U6, | RFM95W-915S2 | RFM95W-915S2 | RF_Module:HOPERF_RFM9XW_SMD | Low power long range transceiver module, SPI and parallel interface, 915 MHz, spreading factor 6 to12 | Digi-Key | RFM95W-915S2-ND | 1
U7, | BMP280 | BMP280 | Package_LGA:Bosch_LGA-8_2x2.5mm_P0.65mm_ClockwisePinNumbering | Absolute Barometric Pressure Sensor, LGA-8 | Digi-Key | 828-1064-1-ND | 2

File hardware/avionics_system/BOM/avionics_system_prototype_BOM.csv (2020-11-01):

Digikey |  |  | Stock Number
Quantity | Part Number | Description
1 | Adafruit BMP280 Breakout Board | Breakout board for BMP280 (barometer) | 1597-1386-ND
1 | Adafruit BNO055 Absoluite Orientation Sensor | Breakout board for BNO055 | 1528-1426-ND
1 | M5Stack Neo-m8n breakout with antenna | Breakout board for Neo-m8n GPS module with antenna | 2221-M003-ND
1 | Micro SD card module | Micro SD card breakout | 1738-1038-ND
RS Online
Quantity | Part Number | Description | Stock Number
2 | Adafruit Lora Radio Breakout Board 433MHz | Adafruit radio transceiver breakout board with RFM96W at 433MHz | 124-5502
RC Hobbies NZ
Quantity | Part Number | Description | Stock Number
1 | Tattu 2S 800mah Lipo Battery |  | TA800-2S45-JST
Jaycar
3 | Arduino Compatible 9G Micro Servo Motor | Micro servo | YM2758
Aerospace Education
Quantity | Part Number | Description | Link
1 | Phenolic Tube 29mm | Body tube for model rocket | http://www.aerospaceeducation.co.nz/gallery/Body%2BTubes%252FAirframes/phenolic-tube-29mm/336322
Somewhere? Is out of stock in a lot of places, but in stock on Adafruits website, not sure how long shipping will take
Quantity | Part Number | Description | Stock Number
1 | Adafruit Feather STM32F405 | Microcontroller breakout board using the STM32F405 microcontroller

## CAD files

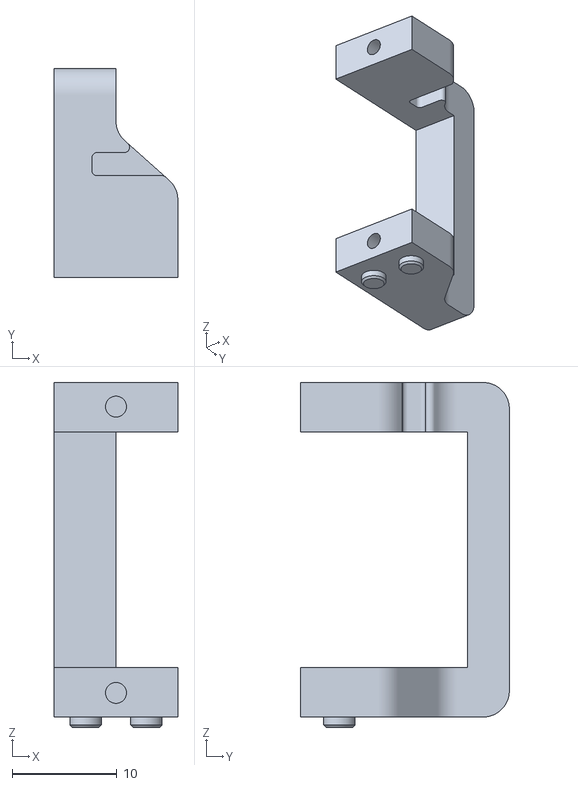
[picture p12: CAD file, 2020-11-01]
hardware/3D_models/gimbal/stl/partials/swivel_servo_a.stl
11.8 x 19.9 x 32.9

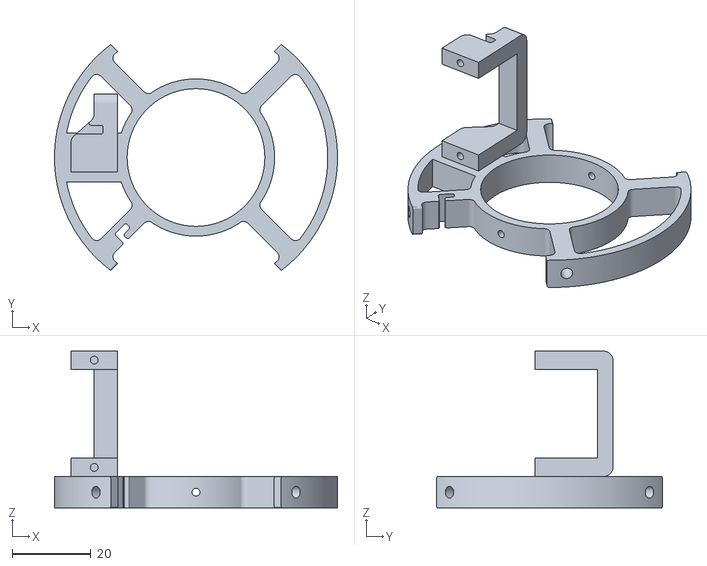
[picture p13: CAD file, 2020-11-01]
hardware/3D_models/gimbal/stl/swivel_b.stl
72.0 x 57.5 x 39.9

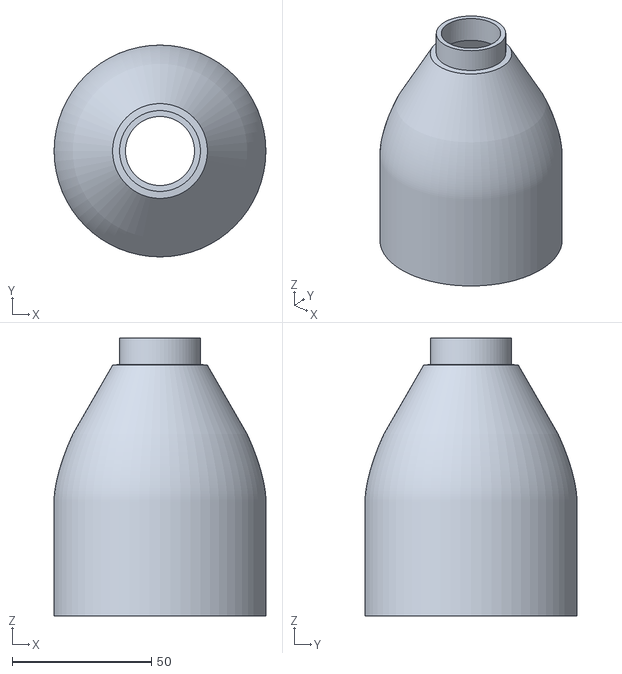
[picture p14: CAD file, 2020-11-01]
hardware/3D_models/gimbal_adaptor/gimbal adaptor.stl
76.0 x 76.0 x 99.7

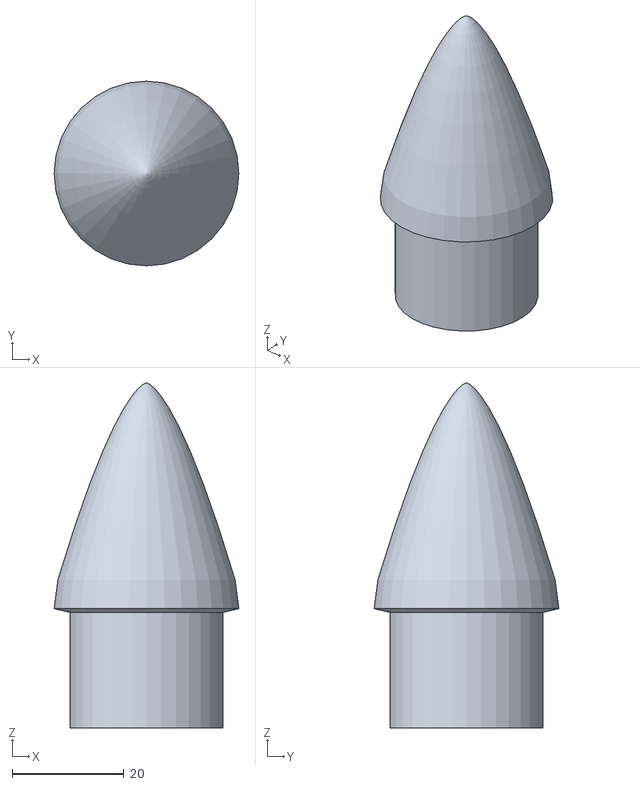
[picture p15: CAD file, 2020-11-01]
hardware/3D_models/nose_cone/nose_cone.stl
33.0 x 33.0 x 61.6

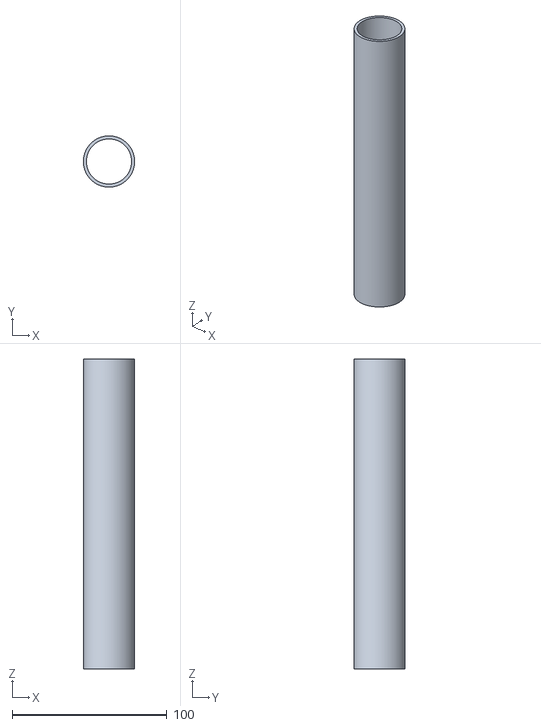
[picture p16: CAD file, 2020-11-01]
hardware/3D_models/rocket_body/rocket tube.stl
33.1 x 33.1 x 200.0

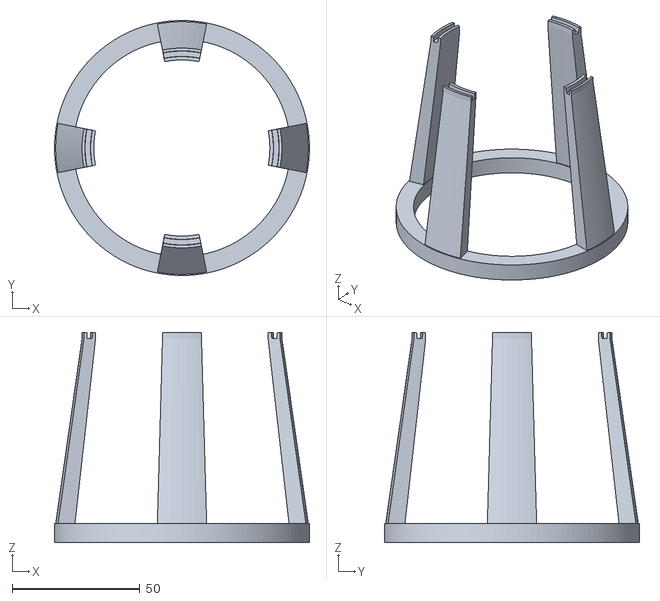
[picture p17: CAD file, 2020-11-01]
hardware/3D_models/rocket_stand/rocket_stand.stl
100.0 x 100.0 x 82.5

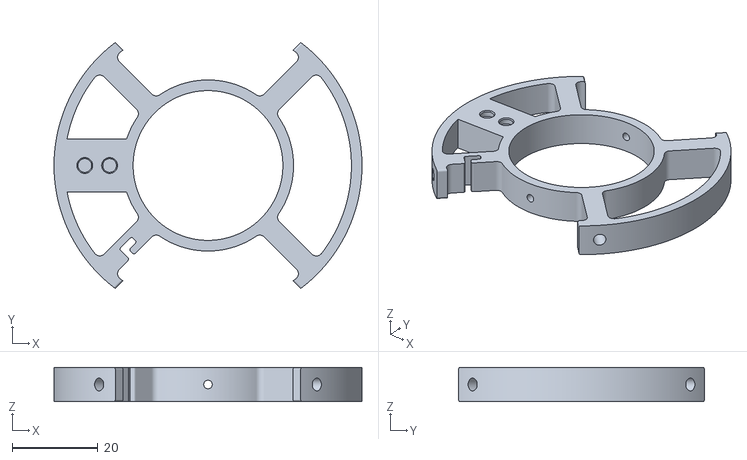
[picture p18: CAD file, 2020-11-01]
hardware/3D_models/gimbal/stl/partials/swivel_b_partial.stl
72.0 x 57.5 x 8.00

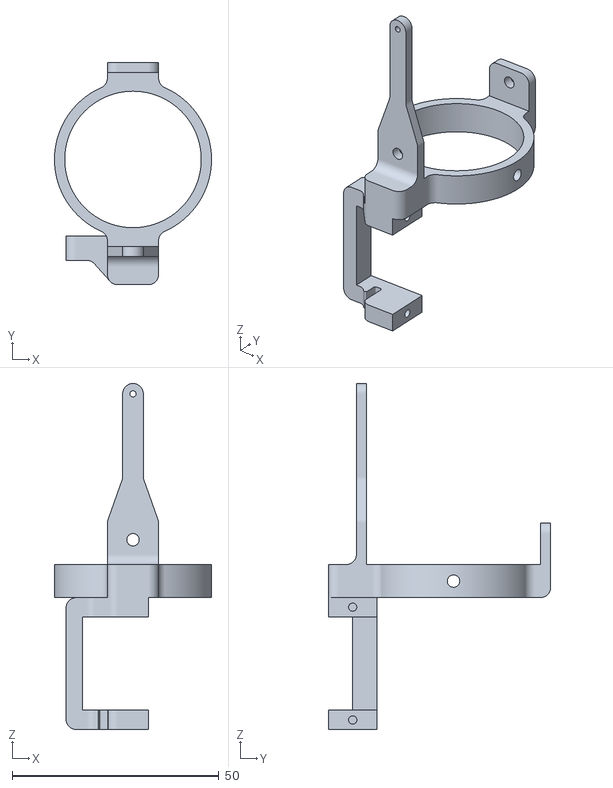
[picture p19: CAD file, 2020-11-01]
hardware/3D_models/gimbal/stl/swivel_a.stl
38.0 x 53.8 x 83.7

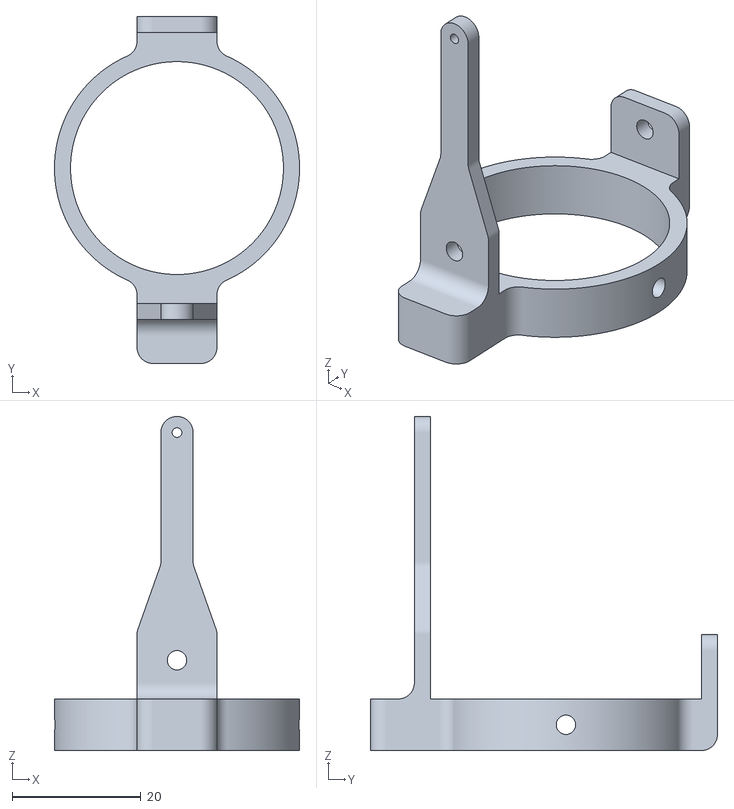
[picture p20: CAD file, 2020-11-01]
hardware/3D_models/gimbal/stl/partials/swivel_a_partial.stl
38.0 x 53.8 x 51.8

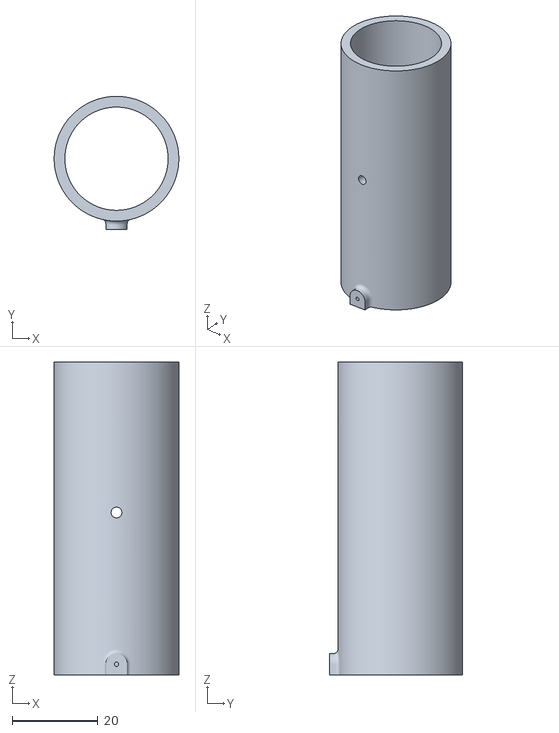
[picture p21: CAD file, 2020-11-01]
hardware/3D_models/gimbal/stl/rocket_mount.stl
29.0 x 31.0 x 72.8

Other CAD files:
hardware/3D_models/gimbal/stl/partials/swivel_servo_b.stl
hardware/3D_models/gimbal/final_design/gimbal.blend
hardware/3D_models/gimbal_adaptor/gimbal_adaptor.blend
hardware/3D_models/rocket_body/rocket tube.blend
hardware/3D_models/rocket_stand/rocket_stand.blend

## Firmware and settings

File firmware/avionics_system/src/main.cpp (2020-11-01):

//Arduino Source Library
#include <Arduino.h>

//Necessary C Libraries
#include <stdint.h>
#include <iostream>

//Required .hh Files
#include "init/init_system.hh"
#include "init/init_test.hh" 
#include "sensor/sensor_battery.hh"
#include "sensor/sensor_gps.hh"
#include "sensor/sensor_barometer.hh"
#include "sensor/sensor_accelerometer.hh"
#include "sensor/sensor_temp.hh"
#include "pre_flight/launch_sequence.hh"
#include "pre_flight/ignition.hh"
#include "launch/flight.hh"
#include "post_flight/post_flight.hh"
#include "led/led_controller.hh"
#include "state/state.hh"

using namespace state_ns;

/////////////////////////////////
/*Variables and Constants*/
/////////////////////////////////

#define MAIN_BUFFER_SIZE 100 //Temporary Value
static const bool isTesting = true;

static uint8_t launch_sequence_passed_tests = 0;
static int battery_pin_number = 0; //TODO:: Adjust this later with the actual pin
static bool hasUploadedFail = false;

/////////////////////////////////
/*Functions*/
/////////////////////////////////

/**
 * Sets up the sensors.
 */
uint8_t setup_sensors() {

  /*Initialisation*/
  int sensorErrorValue = 0;

  /*Setup Battery Sensor*/
  sensorErrorValue = sensor_battery_ns::init_battery(battery_pin_number);
  if (sensorErrorValue > 0) {
    return sensorErrorValue ;
  }

  /*Setup GPS*/
  sensorErrorValue = sensor_gps_ns::init_gps();
  if (sensorErrorValue > 0) {
    return sensorErrorValue;
  }

  /*Setup Barometer*/
  sensorErrorValue = sensor_barometer_ns::init_barometer();
  if (sensorErrorValue > 0) {
    return sensorErrorValue;
  }

  /*Setup Temp*/
  sensorErrorValue = sensor_temp_ns::init_temp();
  if (sensorErrorValue > 0) {
    return sensorErrorValue;
  }

  /*Setup Accelerometer*/
  sensorErrorValue = sensor_accelerometer_ns::init_accelerometer();
  if (sensorErrorValue > 0) {
    return sensorErrorValue;
  }

  /*Success Return as all sensors have passed*/
  return 0;
}

/**
 * Forces the state into failure.
 */
int state_fail() {
  current_state = state::fail;
  return 0;
}

/**
 * Displays the LED on the chip with the colour corresponding to the state that the rocket is in.
 */
int activate_state_led() {

  switch(current_state) {

    case (state::initialisation): {
      //Initialisation => Orange
      led_controller_ns::solid_colour(200, 200, 20, led_controller_ns::led::chip_led);
      break;
    } case (state::test): {
      //Test => Yellow
      led_controller_ns::solid_colour(100, 100, 0, led_controller_ns::led::chip_led);
      break;
    } case (state::idle): {
      //Idle => Green
      led_controller_ns::solid_colour(0, 255, 0, led_controller_ns::led::chip_led);
      break;
    } case (state::launch_sequence): {
      //Launch Sequence => Cyan
      led_controller_ns::solid_colour(0, 255, 255, led_controller_ns::led::chip_led);
      break;
    } case (state::ignition): {
      //Ignition => Blue
      led_controller_ns::solid_colour(65, 105, 255, led_controller_ns::led::chip_led);
      break;
    } case (state::flight): {
      //Flight => Purple
      led_controller_ns::solid_colour(153, 50, 204, led_controller_ns::led::chip_led);
      break;
    } case (state::post_flight): {
      //Post Flight => Magenta
      led_controller_ns::solid_colour(255, 0, 255, led_controller_ns::led::chip_led);
      break;
    } case (state::fail): {
      //Fail => Red
      led_controller_ns::solid_colour(255, 0, 0, led_controller_ns::led::chip_led);
      break;
    } case (state::finished): {
      //Finished => Green
      led_controller_ns::solid_colour(0, 255, 0, led_controller_ns::led::chip_led);
      break;
    }
  }
  return 0;
}

int activate_error_led(int error_code) {
  switch(error_code) {
    case (init_test_ns::failure_code::battery_failure): {
      //Colour => Cyan
      blink_colour(0, 255, 255, 1, led_controller_ns::led::chip_led);
      break; 
    } case (init_test_ns::failure_code::gps_failure): {
      //Colour => Mauve (Purple/Brown)
      blink_colour(0, 176, 0, 1, led_controller_ns::led::chip_led); 
      // blink_colour(224, 176, 255, 1, led_controller_ns::led::chip_led); 
      break;
    } case (init_test_ns::failure_code::accelerometer_failure): {
      //Colour => Chartreuse (Yellow)
      blink_colour(127, 255, 0, 1, led_controller_ns::led::chip_led);      
      break; 
    } case (init_test_ns::failure_code::barometer_failure): {
      //Colour => Teal
      blink_colour(0, 128, 129, 1, led_controller_ns::led::chip_led); 
      break;
    } case (init_test_ns::failure_code::temp_failure): {
      //Colour => Russet (Brown)
      blink_colour(128, 70, 27, 1, led_controller_ns::led::chip_led); 
      break;
    } case (init_test_ns::failure_code::radio_link_failure): {
      //Colour => White
      blink_colour(255, 255, 255, 1, led_controller_ns::led::chip_led); 
      break;
    } case (init_test_ns::failure_code::gimbal_failure): {
      //Colour => Hot Pink
      blink_colour(255, 69, 105, 1, led_controller_ns::led::chip_led); 
      break;
    } case (init_test_ns::failure_code::black_box_failure): {
      //Colour => Glaucous (Dull BLue)
      blink_colour(96, 130, 182, 1, led_controller_ns::led::chip_led);   
      break;
    }

  }
  return 0;
}

/**
  * Gets the next state that the system would be at
  */
int next_state_2() {

  led_controller_ns::blink_colour(5,0,0,1,led_controller_ns::led::chip_led);

  switch(state_ns::current_state) {
    case (state_ns::state::initialisation)  : {state_ns::current_state = state_ns::state::test; break;}
    case (state_ns::state::test)            : {state_ns::current_state = state_ns::state::idle; break;}
    case (state_ns::state::idle)            : {state_ns::current_state = state_ns::state::launch_sequence; break;}
    case (state_ns::state::launch_sequence) : {state_ns::current_state = state_ns::state::ignition; break;}
    case (state_ns::state::ignition)        : {state_ns::current_state = state_ns::state::flight; break;}
    case (state_ns::state::flight)          : {state_ns::current_state = state_ns::state::post_flight; break;}
    case (state_ns::state::post_flight)     : {state_ns::current_state = state_ns::state::finished; break;}
    case (state_ns::state::finished)        : {break;} //Should not change state after already being launched
    case (state_ns::state::fail)            : {break;} //Should not change state after failing
  }
  
  led_controller_ns::blink_colour(5,0,0,1,led_controller_ns::led::chip_led);
  return current_state;
}

/////////////////////////////////
/*Loop and Setup*/
/////////////////////////////////

/**
 * The Main Loop of the System.
 * This should go through all the different states (phases) during the rocket's duration.
 * See https://gitlab.ecs.vuw.ac.nz/course-work/engr300/2020/group2/group-2/-/blob/master/architecture_design/images/4.1_class_diagram.png
 */
void loop() {
  
  //Display the Current State via LED: Blink Solid Blue x4, then State Colour
  blink_colour(0, 0, 255, 4, led_controller_ns::led::chip_led);

  activate_state_led();

  //Perform Current State Actions
  switch(current_state) {
    
    case (state::initialisation): {
      
      init_system_ns::init_loop();
      next_state_2(); 
      break;
      
    } case (state::test): {

      int testReturnValue = init_test_ns::perform_all_tests();
      if (testReturnValue == 0) {
        blink_colour(0, 255, 0, 1, led_controller_ns::led::chip_led); 
        //Should only pass given all the tests pass
        next_state_2();
        activate_state_led();
      } else {
        // blink_colour(0, 128, 0, 1, led_controller_ns::led::chip_led); 
        activate_error_led(testReturnValue);
      }
      break;

    } case (state::launch_sequence): {
      
        //Check if tests have been performed or not. This should olnly be ever called once.
        if (launch_sequence_passed_tests == 0) {
        //Perform Launch Tests
        if (launch_sequence_ns::perform_launch_tests() > 0) {
          current_state = state::fail;
          break;
        }
        launch_sequence_passed_tests = 1;
        launch_sequence_ns::init_start_time();
      }

      //Check the Radio Buffer for "Abort Launch" Commands
      //TODO::

      //Check the Countdown
      if (launch_sequence_ns::countdown_tick() == true) {
        next_state_2();
      }

      break;

    } case (state::ignition): {

      ignition_ns::ignite_launch();
      next_state_2();
      break;

    } case (state::flight): {

      flight_ns::fly_state testReturnValue = flight_ns::launch_loop();

      //Once the rocket has reached the apex, move to post_flight state
      if (testReturnValue == flight_ns::fly_state::APEX) { 
        next_state_2();
      }
      break;

    } case (state::post_flight): {

      post_flight_ns::post_state testReturnValue = post_flight_ns::post_flight_loop();

      //Once the rocket has reached the apex, move to post_flight state
      if (testReturnValue == post_flight_ns::post_state::GROUNDED) {
        next_state_2();
      }
      break;

    } case (state::idle): {
      
      //Check for Software Start
      if (true /*TODO::*/) {
        next_state_2();
      }
      break;

    } case (state::fail): {

      if (!hasUploadedFail) {
        //Upload Fail Data to blackbox here.
        hasUploadedFail = true;
      }
      break;

    } case (state::finished) : {

      break;

    }
  }

}

/**
 * The first function to be called.
 * It should set up the sensors as best as it can.
 * If there is a setup failure, it should return early, and set the rocket to a fail state.
 */
void setup() {

  // Serial.begin(9600);
  led_controller_ns::setup_leds();
  
  //Blink Red 10 times for SetUp
  blink_colour(255, 0, 0, 10, led_controller_ns::led::chip_led); 
  // blink_colour(255, 0, 0, 1, led_controller_ns::led::chip_led); 

  switch (setup_sensors()) {

    case (10): {
      //GPS Failure
      current_state = state::fail;
      print_state();
      return;
    } case 20: {
      //Barometer Failure
      current_state = state::fail;
      print_state();
      return;
    } case 30: {
      //Temperature Failure
      current_state = state::fail;
      print_state();
      return;
    } case 40:  {
      //Accelerometer Failure
      current_state = state::fail;
      print_state();
      return;
    }
    default:
      break;
  }

  /*Set the initial current_state given no failures*/
  // current_state = state::initialisation;
  current_state = state::initialisation;
  print_state();

  //Blink Green 10 Times after Setup for a "Passed" SetUp
  // blink_colour(0, 255, 0, 1, led_controller_ns::led::chip_led);
  blink_colour(0, 255, 0, 10, led_controller_ns::led::chip_led);
}

/*Uncomment out for native testing*/
// int main(void) {
//   setup();
//   while(true) {
//     loop();
//   }
// }

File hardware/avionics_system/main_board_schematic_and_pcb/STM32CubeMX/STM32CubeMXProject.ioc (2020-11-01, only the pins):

Mcu.UserName=STM32F405RGTx
PA0-WKUP.Signal=GPIO_Analog
PA1.Signal=GPIO_Output
PA10.Signal=USB_OTG_FS_ID
PA11.Signal=USB_OTG_FS_DM
PA12.Signal=USB_OTG_FS_DP
PA13.Signal=SYS_JTMS-SWDIO
PA14.Signal=SYS_JTCK-SWCLK
PA2.Signal=USART2_TX
PA3.Signal=USART2_RX
PA4.Signal=SPI1_NSS
PA5.Signal=SPI1_SCK
PA6.Signal=SPI1_MISO
PA7.Signal=SPI1_MOSI
PA8.Signal=GPIO_Input
PA9.Signal=USB_OTG_FS_VBUS
PB0.Signal=S_TIM3_CH3
PB1.Signal=S_TIM3_CH4
PB10.Signal=I2C2_SCL
PB11.Signal=I2C2_SDA
PB12.Signal=SPI2_NSS
PB13.Signal=SPI2_SCK
PB14.Signal=SPI2_MISO
PB15.Signal=SPI2_MOSI
PB2.Signal=EVENTOUT
PB3.Signal=SYS_JTDO-SWO
PB5.Signal=GPIO_Output
PB6.Signal=GPIO_Output
PB7.Signal=GPIO_Output
PB9.Signal=GPIO_Input
PC10.Signal=SDIO_D2
PC11.Signal=SDIO_D3
PC12.Signal=SDIO_CK
PC15-OSC32_OUT.Signal=GPIO_Output
PC4.Signal=GPIO_Input
PC5.Signal=GPIO_Input
PC6.Signal=USART6_TX
PC7.Signal=USART6_RX
PC8.Signal=SDIO_D0
PC9.Signal=SDIO_D1
PD2.Signal=SDIO_CMD

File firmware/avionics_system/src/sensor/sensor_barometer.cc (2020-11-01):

#include "sensor_barometer.hh" 
#include <Wire.h>
#include <SPI.h>
#include <Adafruit_BMP280.h>
#include "sensor.cc"

#define BMP_SCK 23
#define BMP_MISO 24
#define BMP_MOSI 25
#define BMP_CS 11

// Adafruit_BMP280 bmp; // use I2C interface
Adafruit_BMP280 bmp(BMP_CS, BMP_MOSI, BMP_MISO, BMP_SCK);
Adafruit_Sensor *bmp_temp = bmp.getTemperatureSensor(); //currently unused, not part of MVP
Adafruit_Sensor *bmp_pressure = bmp.getPressureSensor();

/*Functions*/
/**
* Initialises barometer. Returns a status code.
*/
int sensor_barometer_ns::init_barometer() {
  // Perform some initialisation of the sensor

  // //Commented Out because it doesn't work
  // Serial.begin(9600);
  // if (!bmp.begin()) {
  //   Serial.println(F("BMP280 Sensor Initialisation failed."));
  //   return 1; //failure!
  // }

  // //TODO: Check if sampling settings are appropriate
  // bmp.setSampling(Adafruit_BMP280::MODE_NORMAL,     /* Operating Mode. */
  //                 Adafruit_BMP280::SAMPLING_X2,     /* Temp. oversampling */
  //                 Adafruit_BMP280::SAMPLING_X16,    /* Pressure oversampling */
  //                 Adafruit_BMP280::FILTER_X16,      /* Filtering. */
  //                 Adafruit_BMP280::STANDBY_MS_500); /* Standby time. */

  // circ_buff_barometer = new sensor_ns::circular_buffer<int>;

  return 0; //success!
}

/**
  * Prompts the sensor to collect data, and record it to its buffer.
  */
int sensor_barometer_ns::record_data_barometer() {
  //Record the data, and add it to the buffer
  // sensors_event_t pressure_event;
  // if(!bmp_pressure->getEvent(&pressure_event)) {
  //   //TODO: Add proper fail state 
  //   return 1; //Getting pressure failed
  // } 
  // circ_buff_barometer->addValue(pressure_event.pressure);
  return 0;

}


int sensor_barometer_ns::get_data_barometer(sensor_barometer_ns::barometer_data_t* return_data) {
  //Get Head of the Data
  // if(circ_buff_barometer == nullptr || circ_buff_barometer->getBuffer() == nullptr){
  //   return 1;
  // }
  // int* pressure_value = circ_buff_barometer->getBuffer();
  // return_data->pressure = *pressure_value;
  return 0;
}
  
